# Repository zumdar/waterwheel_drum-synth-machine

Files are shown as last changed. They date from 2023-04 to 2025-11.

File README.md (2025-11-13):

# The Wacky Waterwheel Wonder Machine!

A synthesizer, drum machine, electromechanical, waterwheel powered musical intsrument!

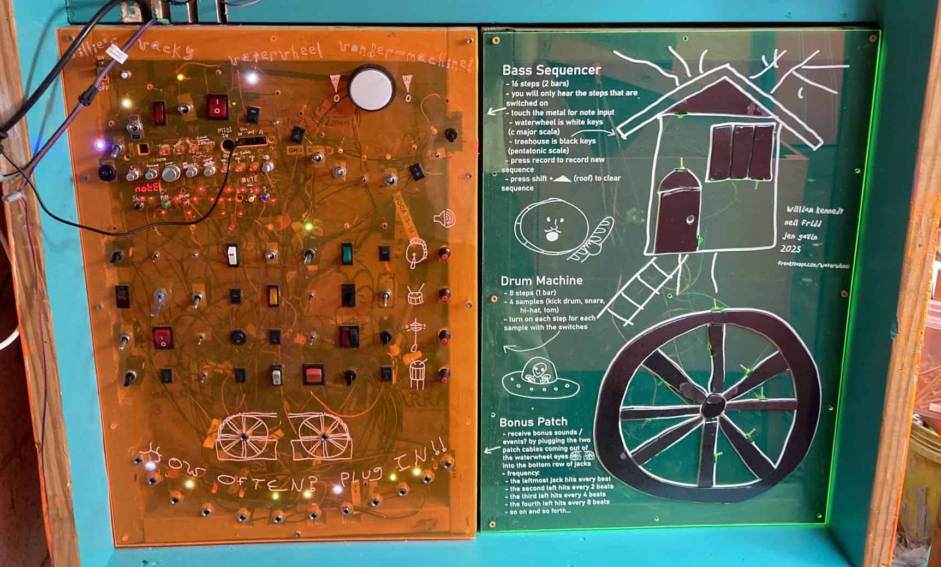
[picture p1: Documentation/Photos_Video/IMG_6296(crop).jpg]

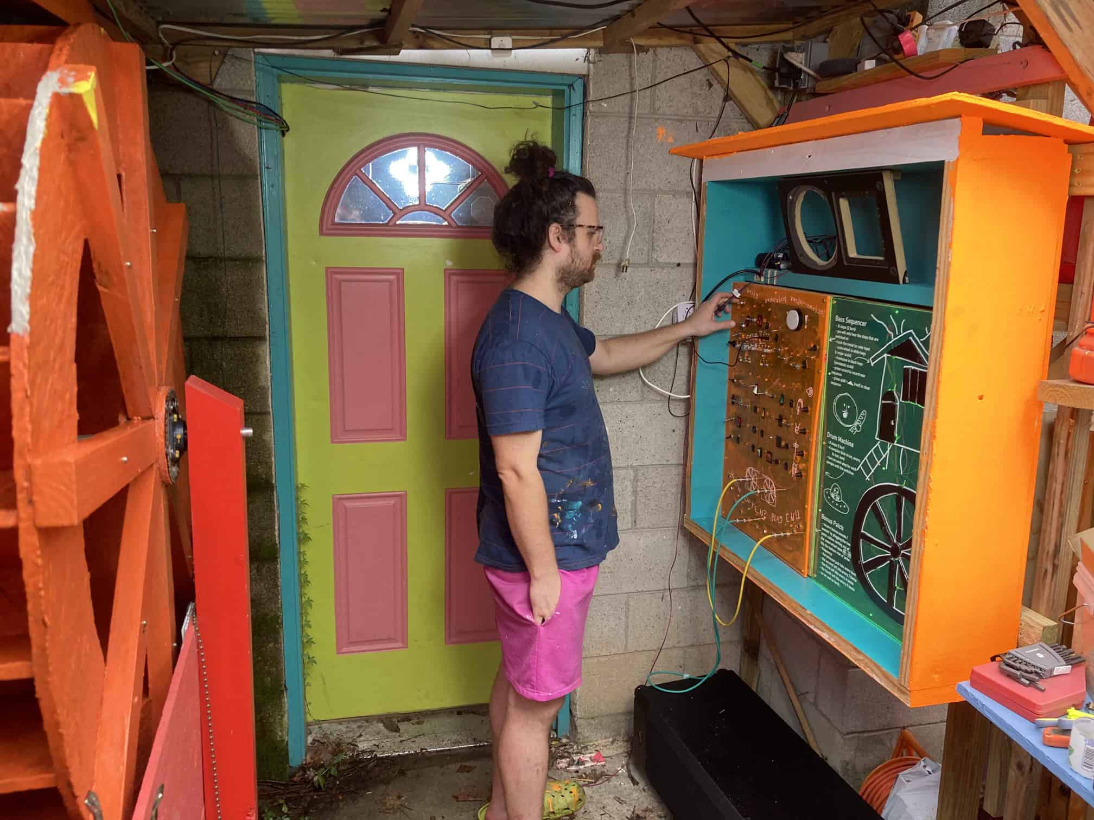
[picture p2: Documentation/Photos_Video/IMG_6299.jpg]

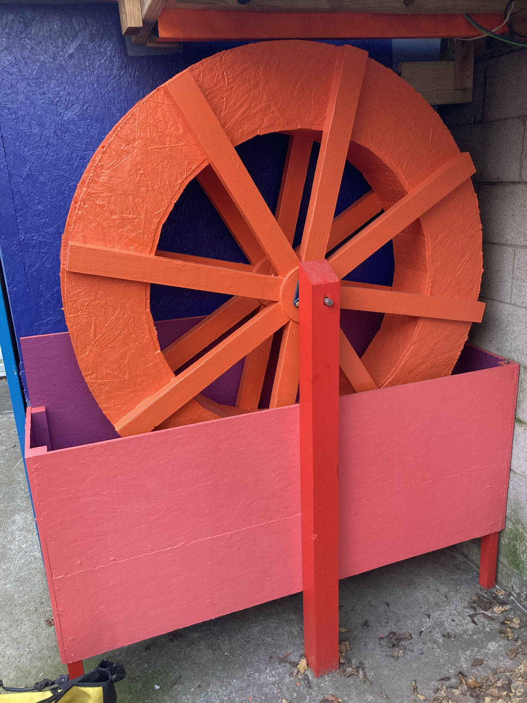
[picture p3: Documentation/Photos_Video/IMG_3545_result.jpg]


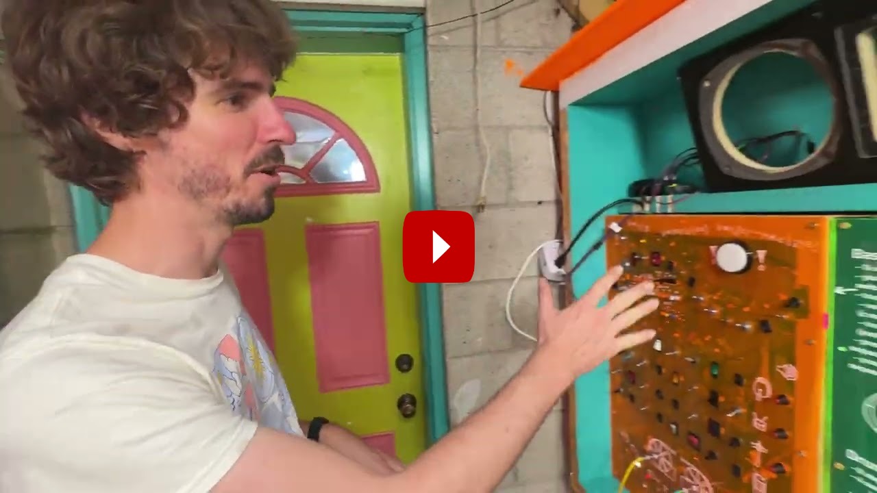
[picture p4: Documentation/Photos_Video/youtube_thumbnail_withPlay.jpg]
youtube link (https://www.youtube.com/watch?v=vC32thTY1A0)


Started in Oct. 2022 in Nashville, TN as part of The Paradise Driveway residency, full working version complete in Oct. 2025.

Project created in collaboration with

- [Neil Fridd (aka Terror Pigeon)](https://terrorpigeon.bandcamp.com/)
- [Jen Gavin (aka Paradise MIDI)](https://paradisemidi.com/)

# Overview

The Waterwheel Wondermachine is a nature powered mechanical-electronic logic idea workstation. It is a hybrid of bass synthesizer, drum machine, and kinetic motor instrument. When it rains, the waterwheel spins and every spoke of the wheel triggers the machine to advance one step of the sequence.

It has the feel of an old analog switch board or the cockpit of an airplane with 50+ toggle switches, patch cables, and LEDs scattered everywhere. Intimidating as it may look from the outside — and even more so on the inside since the front panels are translucent — the machine is simple enough where anyone can walk up and play it!

When it rains, the machine generates evolving musical sequences mixed with the percussive sounds of the external motors striking parts of the frame. When the sun returns, it transforms into a contemplative sound sculpture, droning notes played on the touch canvas panel.

You can play a melody on the waterwheel drawing, using its cleverly arranged key sequence to inspire a new variation on the original idea. All of this is contingent on the correct environmental conditions (rain), so that you have a consistent performance. The rain sounds also play a sonic role, incorporating into the spacial ambiance.

# Tech Specs

- 16 step bass synthesizer sequencer
- 8 step, 4 sample drum sequencer
- 2x motor outputs, motors mounted in the instrument area, creating sounds by clever mounting with the motors hitting parts of the frame.
- All timing and sequencing done with CD4xxx logic chips and digital circuity, a complex puzzle of logic chips, inputs and outputs and buffering.
- the note input of the synthesizer is a drawing of a waterwheel and tree house (homage to Neil s backyard). We cut these pieces out of metal and are using capacitive touch to send those notes to the synthesizer.
- 1 big sample button to trigger a sample whenever the performer wants

# PCB

## V1 - etched

- Schematic was designed in October 2022. A PCB (well 3 actually...) were designed and then etched on the driveway on copper clad FR4 board. Here is the design:
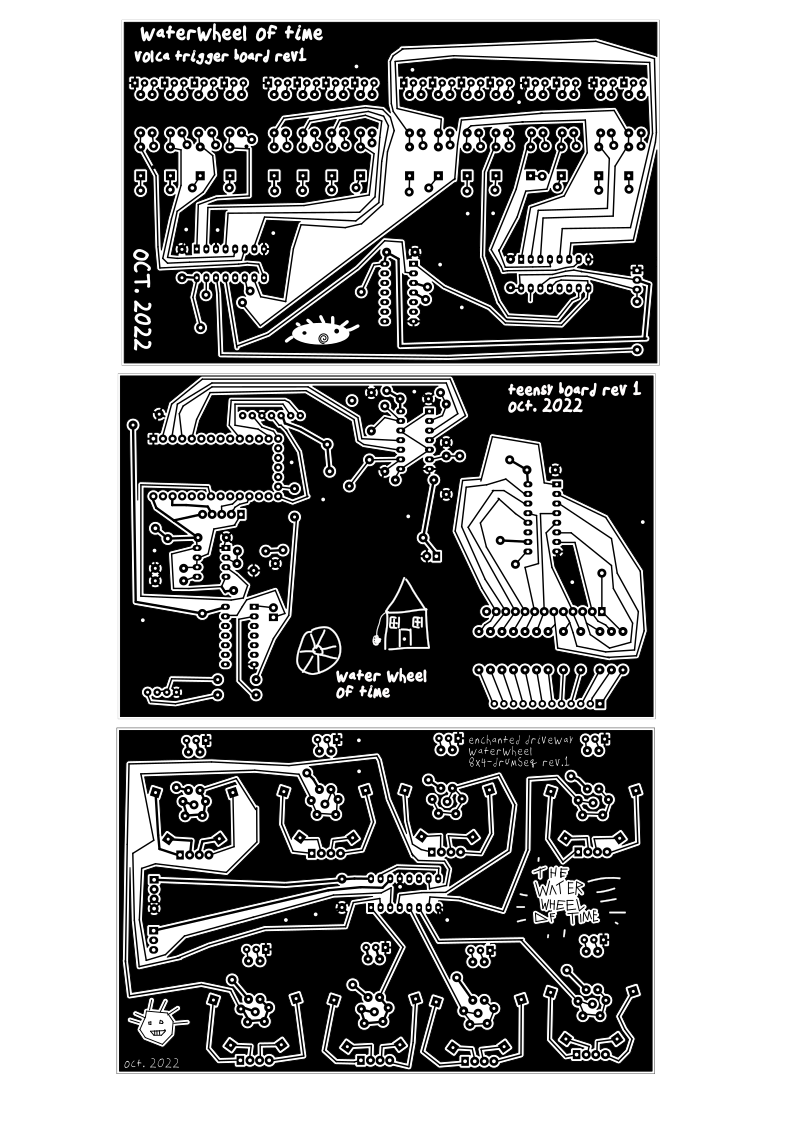
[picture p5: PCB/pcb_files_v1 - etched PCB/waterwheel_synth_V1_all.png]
  
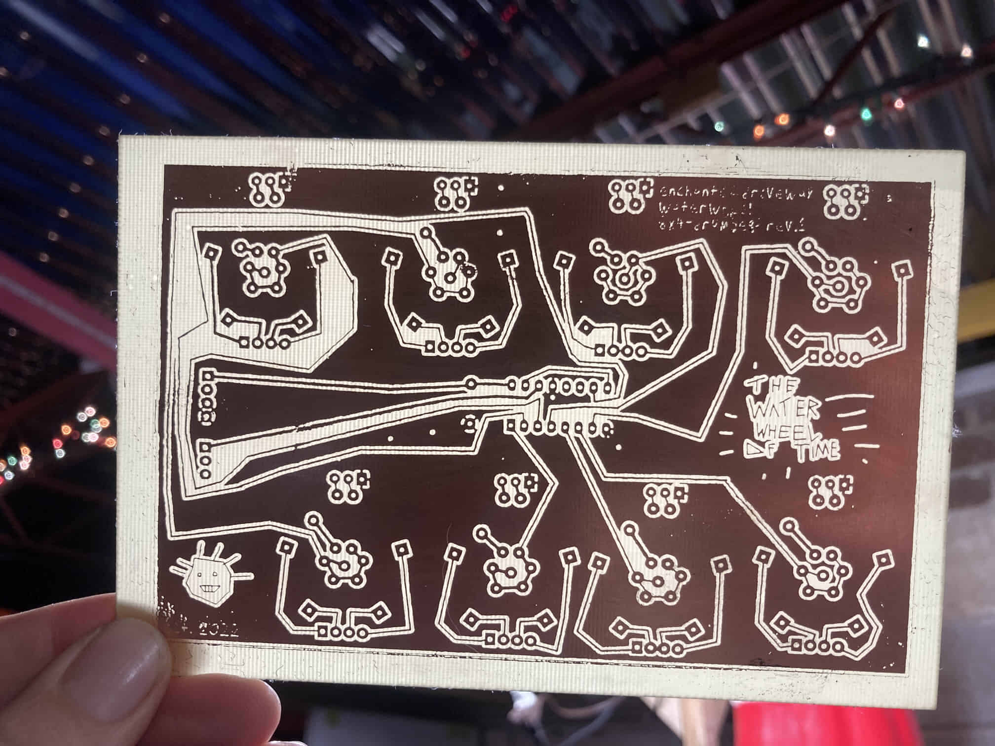
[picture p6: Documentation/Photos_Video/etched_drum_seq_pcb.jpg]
  
- The etched PCB was tested and then a full PCB was designed and fabricated by JLCPCB

## V2 - fabricated PCB

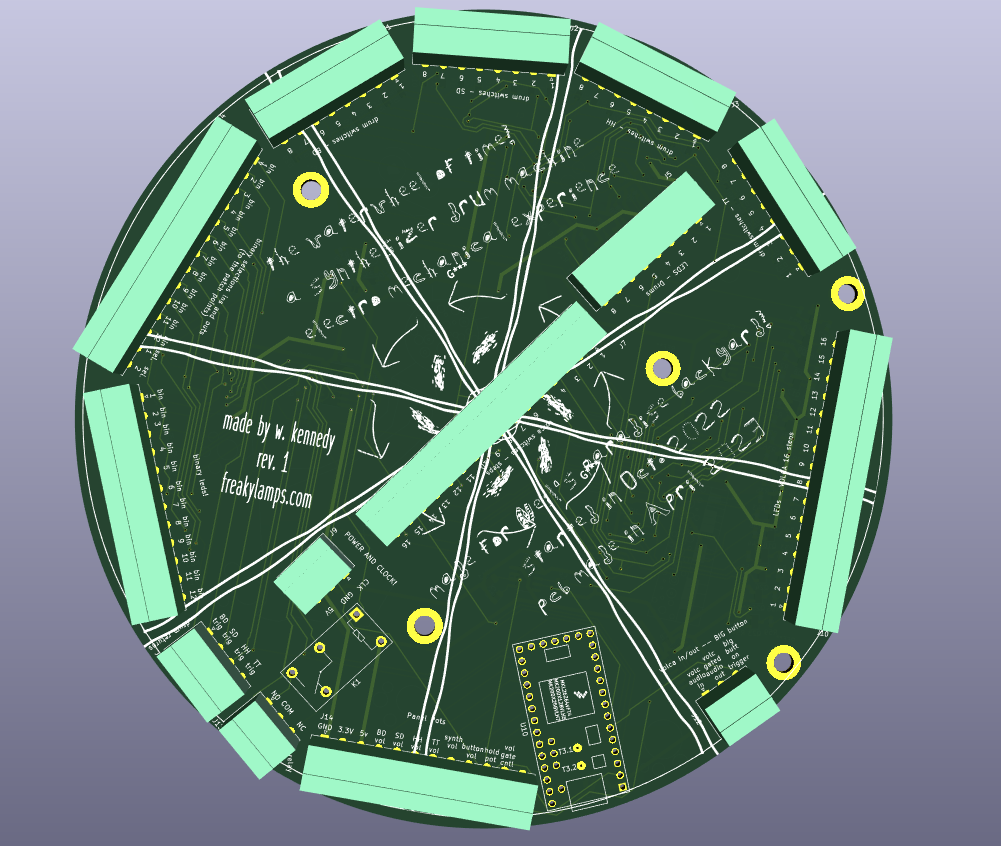
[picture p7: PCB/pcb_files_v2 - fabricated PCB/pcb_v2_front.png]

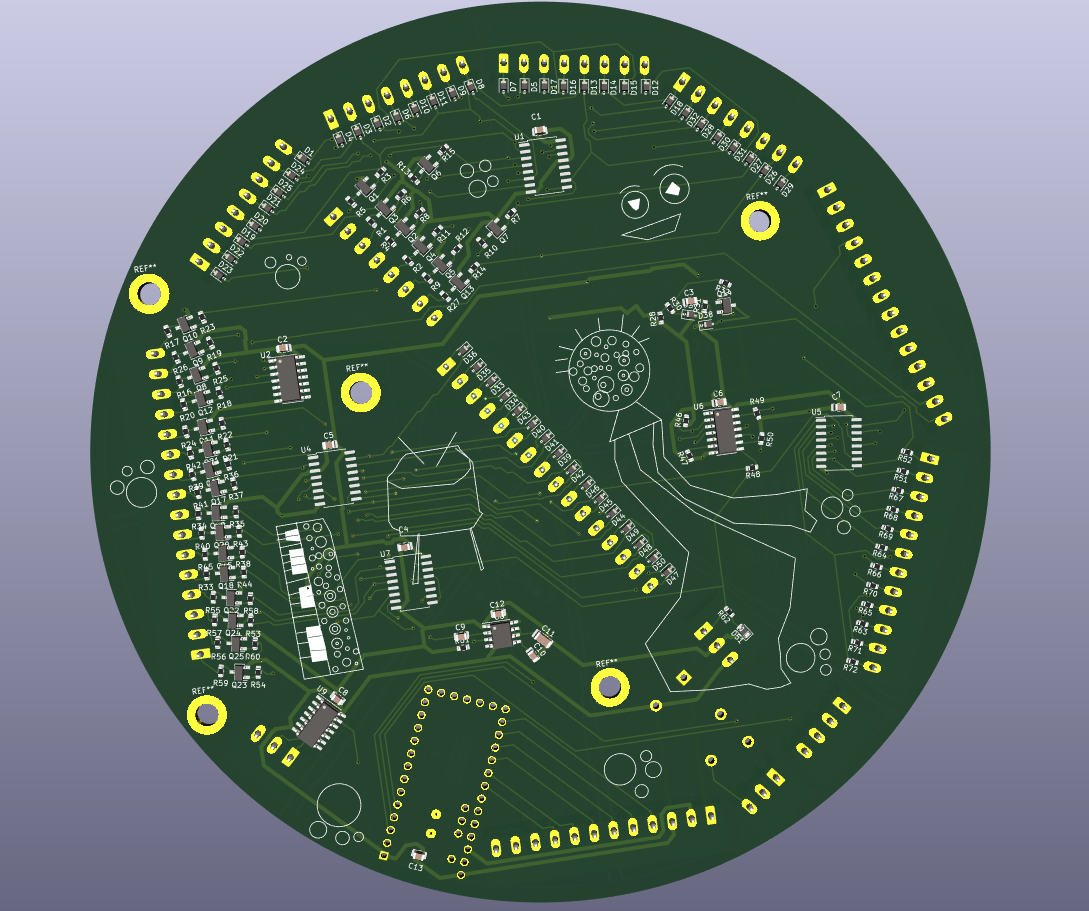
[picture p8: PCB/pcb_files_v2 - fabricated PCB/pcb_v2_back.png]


[Link to Schematic for V2](https://github.com/zumdar/waterwheel_drum-synth-machine/blob/main/PCB/pcb_files_v2%20-%20fabricated%20PCB/waterwhel_V2_SCHEMATIC.pdf)

## PCB V2 errors

- no pulldown for clock
- 555 footprint doesnt fit
- some silkscreen labels are covered up by connectors

# References

[getting trigger from sequencer - casper electronics ](https://web.archive.org/web/20130509102109/http://casperelectronics.com/2007/03/19/sequencer-update/)

[more info about multi channel 4017 sequencer/trigger - sailor mouth](https://web.archive.org/web/20160915053601/http://www.sailormouth.org/trigseq2.html)

[how to get a easy trigger with the 4017 sequecner - little gate seq - electro music forum](https://electro-music.com/forum/topic-63020.html)

[MFOS 4017 sequencer lots of good info on how it works](http://musicfromouterspace.com/analogsynth_new/TENSTEPSEQUENCER/TENSTEPSEQUENCER.php)

[classic baby 10 sequencer](https://hackaday.com/2016/01/14/oh-baby-baby10-build-a-classic-analog-music-sequencer/)

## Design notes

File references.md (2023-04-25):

# Notes about Waterwheel Synthesizer project

DAY 1
 - experiement with old Volca Keys and Bass, 
 - come up with idea for 64 switches, start working on schematic 

DAY 2 - 
- install reed switch and magnets on wheel
- tweak to get them all working
-  Prototype 4017 sequencer, 2 channel 4 steps each. 
-  need AND circuit to get triggers for each step, use 4093 NAND chip. 
- sucess with sample player with SD card! 
### research
I want sample playback for drum sounds
#### Requirements  
- needs to be quick (adafruit sound fx board takes 125ms to trigger!)
- want to change samples on the fly with sd card or IDEALLY usb stick
- No external hardware other then what i have.. no teensy audio shields
  - esp, arduino, teensy
- [teensy 4.0 sample player](https://forum.aemodular.com/thread/1214/teensy-4-sample-player) - pretty perfect except you need to do the wav to C++ conversion and upload new code for new samples....
- [teensy polyphonic samples](https://github.com/newdigate/teensy-polyphony)
- [teensy variable playback ](https://github.com/newdigate/teensy-variable-playback) - confusing library but you can play back samples.. do you need external audio shield?

## References

[getting trigger from sequencer - casper electronics ](https://web.archive.org/web/20130509102109/http://casperelectronics.com/2007/03/19/sequencer-update/)

[more info about multi channel 4017 sequencer/trigger - sailor mouth](https://web.archive.org/web/20160915053601/http://www.sailormouth.org/trigseq2.html)

[how to get a easy trigger with the 4017 sequecner - little gate seq - electro music forum](https://electro-music.com/forum/topic-63020.html)

[MFOS 4017 sequencer lots of good info on how it works](http://musicfromouterspace.com/analogsynth_new/TENSTEPSEQUENCER/TENSTEPSEQUENCER.php)

[classic baby 10 sequencer](https://hackaday.com/2016/01/14/oh-baby-baby10-build-a-classic-analog-music-sequencer/)

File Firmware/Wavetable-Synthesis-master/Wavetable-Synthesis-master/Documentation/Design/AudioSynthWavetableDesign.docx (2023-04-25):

# AudioSynthWavetable Design Specification

Project: TeensyAudio Wavetable Synthesis

Authors: Ryan Mellmer

Connor Delaplane

Aida Keifer

Nicholas Craig

Josh Bucklin

Jonathan Jensen

Xuan Tang

Date: 2016-11-28

Version: 1.0

Table of Contents

1 INTRODUCTION

1.1 Objectives

1.2 Scope

2 Functionality

2.1 Site Map

3 Architecture

3.1 Architecture Overview

3.2 Application Interfaces

4 Design

4.1 Object Diagram

5 CODE

5.1 File Names and Structure

5.2 Executable File Names and Structure

# 1 INTRODUCTION

## 1.1 Objectives

The purpose of this document is to outline the technical specifications for the Wavetable Synthesis library to be used on the Teensy 3.2 microcontroller. It is primarily meant as a guide for the developers of the library and will cover the following areas:

- Definitions of all objects within the library along with their interfaces.
- Interactions with the existing Audiostream.h library API.

## 1.2 Scope

The purpose of this project is to provide a C++ library and accompanying Python utility scripts allowing realistic instrumentation audio to be synthesized on the Teensy 3.2 Arduino Digital Analog Converter (DAC). This library will be exposed to developers, and will allow pitch shifting, looping, tremolo, and vibrato effects to be imposed on a raw byte buffer of recorded samples.

# 2 Functionality

## 2.1 Soundfont Decoding

The basic functionality of the SoundFont Decoding script is defined in the Wavetable Synthesis on Microcontroller Requirements document. A brief summary is provided here.

- User executes the script in a console
- User loads a .sf2 file into the utility by passing it’s location to the script
- If the .sf2 adheres to pre-defined limitations for what the Wavetable Library accepts, then allow the user to select which instrument to import
- Parse samples into logical units
- Output the resulting samples into a C++ struct/object within a .cpp file for use within the Wavetable Synthesis Library

## 2.2 Wavetable Synthesis Library

The basic functionality of the Wavetable Synthesis Library is defined in the Wavetable Synthesis on Microcontroller Requirements document. A brief summary is provided here.

- Load audio data from the file produced by SF2 extraction process
- Play silence in the event of read error
- Create interpolated audio data on the Teensy
- An audio sample’s sustain data can be looped
- Audio data can be modified with a tremolo effect
- Audio data can be modified with a vibrato effect

# 3 Architecture

## 3.1 Architecture Overview

SF2 file object diagram:

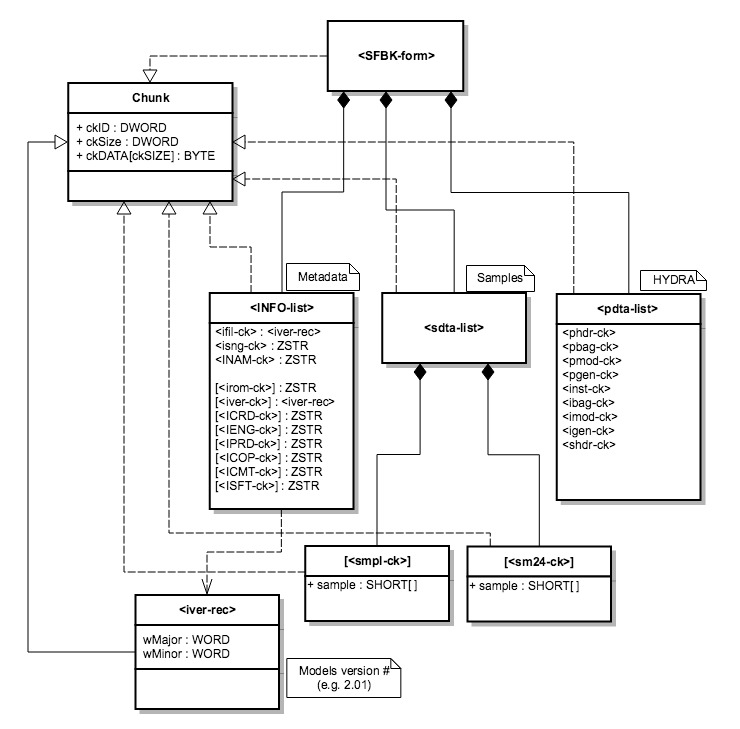
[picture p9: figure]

SoundFont Decoding:

Teensy C++ Library:

This diagram gives a general overview of how both the SF2 Decoder and the Teensy C++ Library will work together. It’s important to notice that a single Note # file generated by the SF2 Decoder will contain all three phases for a single sample (attack, sustain, release). In addition, while there is only a single arrow from the Wavetable to Teensy Sketch there could be up to 10 instances. There should be at least one Wavetable object for every note included in the Teensy Sketch file.

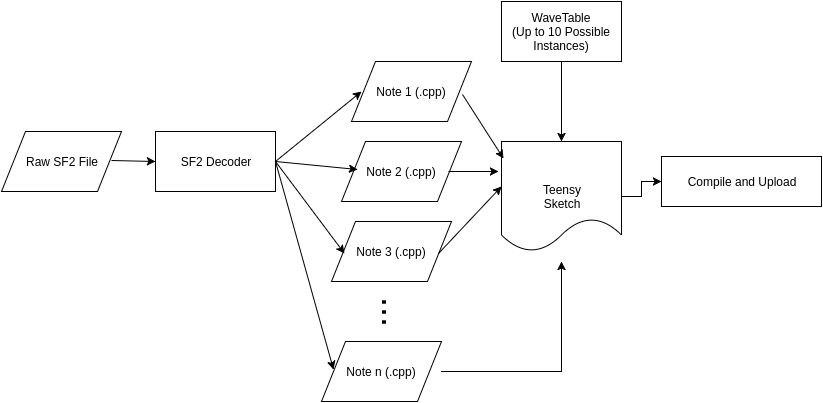
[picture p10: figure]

## 3.2 Application Interfaces

This section contains a description of all SF2 Decoding and Teensy C++ Library application interfaces.

Python SF2 Decoding:

The SoundFont decoding script will be ran only through the command-line, so the only interface to be described is the command-line. The user will need to input the location of the SoundFont file to decode, and the script will walk the user through the decoding process.

Teensy C++ Library:

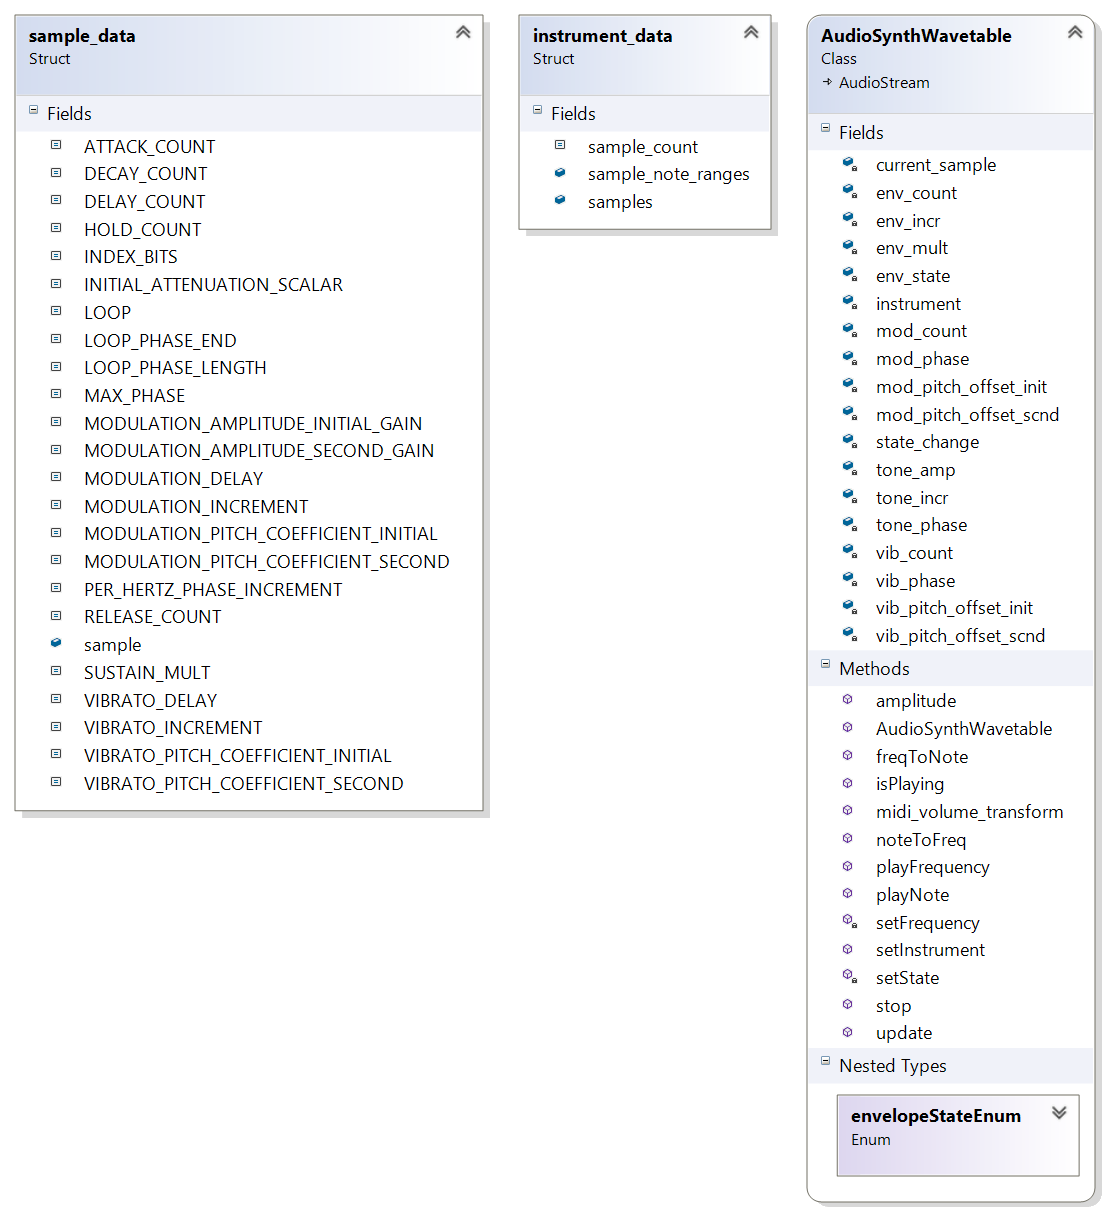
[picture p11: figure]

The AudioSynthWavetable library is made up of 3 distinct datatypes:

1. AudioSynthWavetable Class object
2. instrument_data struct
3. sample_data struct

The AudioSynthWavetable object is the main API object to interface with in order to utelize the wavetable library. This class exposes methods surrounding playing notes, changing frequency of playback, stopping notes, and setting the instrument to play. A complete description of the AudioSynthWavetable class can be found at https://teensyaudio.github.io/Wavetable-Synthesis/html/index.html

The instrument_data struct contains information which makes up a complete instrument, such as an array of samples in the form of sample_data structs, the number of samples for the instrument, and key range upper bounds for each sample within the instrument. The sample_data struct contains information surrounding a specific sample within an instrument. The sample_data information is exported and stored as algebraic expressions as to optimize and reduce the amount of processing that has to be done on the Teensy at runtime as to increase playback efficiency. A full listing of all of the fields within these structs as well as the purpose for their values can be found within the sample_data.cpp file.

# 4 Design

## 4.1 Class Diagrams

Soundfont Decoding:

The SoundFont decoding script will be contained within a single Python file. Since the script will be a purely command-line driven tool, an open source library, sf2utils, will be utilized to assist in the soundfont decoding process.

Teensy C++ Library:

The Wavetable Synthesis library consists of one primary class called AudioSynthWavetable. A class diagram that lists the fields and methods of this class is given above, and documentation for the API specifics is given at https://teensyaudio.github.io/Wavetable-Synthesis/html/index.html

This is followed by a brief description of each element within the diagram. Note: The public methods and their functionality are listed in section 3.2, Application Interfaces.

# 5 CODE

## 5.1 File Names and Structure

This section lists the name, purpose and structure of all expected files for this project.

SoundFont Decoding Utility:

File #1: decoder.py

Purpose: Main Python script file which the user will actually interact with to decode samples from a soundfont file.

Structure: This file will contain the entirety of the necessary functionality for the SF2 decoding script.

Teensy C++ Library:

File #1: AudioSynthWavetable.h

Purpose: This file contains the Wavetable class prototype and is intended to be #include(d) within any file using the Wavetable object.

Structure: This file will contain a single class prototype, Wavetable, that is derived from the AudioStream class. As such the prototype will contain the update() method along with all other fields and methods listed in the Wavetable class diagram found in section 4.1.

In addition to the class prototype the Audiostream.h library will be #include(d) so it is available for the new Wavetable class.

File #2: AudioSynthWavetable.cpp

Purpose: This file contains the implementation of all of the Wavetable class methods.

Structure: This file will #include the Wavetable.h file and will contain implementations for all public and private methods of the class.

Wavetable Synthesis Technical Specification v1.0 Page of

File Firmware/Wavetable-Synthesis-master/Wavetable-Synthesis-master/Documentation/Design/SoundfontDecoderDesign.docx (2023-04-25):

# SoundFont Decoding Functional Specification

## 1. Introduction

### 1.1. Summary

The SoundFont decoding script will be a utility included with the TeensyAudio Wavetable codebase and will allow users to pull data for various instrumentation samples from SoundFont 2 files for use by the TeensyAudio Wavetable library.

### 1.2. Requirements

See requirements documentation for detailed description of the functional requirements this document will implement.

### 1.3. Existing System

Currently this functionality isn’t available to users of the Teensy library. The script to decode SF2 files will be a brand new addition to the TeensyAudio codebase.

### 1.4. Terminology

DAC - Digital Analog Converter (the Teensy 3.2 is an example of a DAC).

SF2 - SoundFont version 2 File Format (wavetable audio data wrapped w/ synthesis methods).

Sample Array - An array or list of individual byte samples to be produced by the SoundFont decoding script for use in the TeensyAudio Wavetable library.

Attack - Portion of the decoded sample array which plays immediately upon activation (e.g. piano key depression).

Sustain - Portion of the decoded sample array which can be looped indefinitely to produce a sustaining, consistent instrument tone.

Release - Portion of the decoded sample array which plays after the sustained section of a note, and will mark the natural end of a tone.

### 1.5. References

# Wavetable Synthesis on Microcontroller Requirements.docx - Rev 115

## 2. Functional Description

Use Cases

1. Load Soundfont/SF2
  1.1. Description: User provides something for the utility to process.
  1.2. Actors: User; Soundfont;
  1.3. Entry Conditions: N/A
  1.4. Exit Conditions: Relevant contents of the Soundfont are displayed on screen in some selectable format.
  1.5. Flow:
    1.5.1. User invokes utility, specifying local file path to desired soundfont/SF2.
    1.5.2. Necessary checking for compatibility and proper file structure is done by the utility. Error and exit program if one of the following scenarios are met:
      1.5.2.1. SF2 file can’t be imported, or a file read issue occurs.
      1.5.2.2. Instrument/sample sections don’t exist within the file.
    1.5.3. Success message displayed to user if compatible.
      1.5.3.1. Failure message displayed to user if Soundfont does not meet the protocol or in the event of a File Read Error.
      1.5.3.2. Exit.
    1.5.4. Continue to Select Instrument.
2. Select Instrument
  2.1. Description: User needs to select an instrument(s) to use.
  2.2. Actors: User; Soundfont;
  2.3. Entry: Soundfont contents are displayed on screen.
  2.4. Exit: User has chosen quit, or finish.
  2.5. Flow:
    2.5.1. A prompt is displayed on screen to select an instrument, otherwise quit.
    2.5.2. User selects quit.
      2.5.2.1. Utility terminates.
    2.5.3. User inputs a selection.
      2.5.3.1. A prompt is displayed on screen to select an additional instrument, finish, or quit.
      2.5.3.2. If User selects an instrument
        2.5.3.2.1. go to 2.5.3.1
      2.5.3.3. If User selects finish
        2.5.3.3.1. Continue to Parse Samples.
      2.5.3.4. If User selects quit.
        2.5.3.4.1. Terminate utility.
3. Parse Sample(s)
  3.1. Description: User selects a sample(s) to export.
  3.2. Actors: User; Soundfont;
  3.3. Entry: Available samples are shown to the user for the selected instrument.
  3.4. Exit: User selects sample(s) to export, then the program continues to export samples.
  3.5. Flow:
    3.5.1. A prompt is displayed on screen to select an sample, otherwise quit.
    3.5.2. User selects quit.
      3.5.2.1. Utility terminates.
    3.5.3. User inputs a selection.
      3.5.3.1. Error and exit program if one of the following scenarios are met:
        3.5.3.1.1. Sample loop-end - loop-start > sample-end - sample-start (Check that the looping section is smaller than the sample itself.
        3.5.3.1.2. Sample loop-end < sample-end (Check that the sample loop end position isn’t past the end of the sample)
      3.5.3.2. If errors have occurred here, then we can potentially do some automated modification to the start and end index locations. Ask the user if they want the program to attempt to fix these issues, or quit.
      3.5.3.3. If no errors, a prompt is displayed on screen to select additional samples (if memory space on Teensy would allow so), finish, or quit.
      3.5.3.4. If User selects another sample
        3.5.3.4.1. Go to 3.5.3.1
      3.5.3.5. If User selects finish
        3.5.3.5.1. Continue to export samples.
      3.5.3.6. If User selects quit.
        3.5.3.6.1. Terminate utility.
4. Export Sample(s)
  4.1. Description: Selected samples get exported/encoded to a .cpp file with corresponding .h file, in either PCM or ulaw sound data encoding.
  4.2. Actors: User; Soundfont;
  4.3. Entry: Desired samples have been chosen for export.
  4.4. Exit: Program generates a corresponding .cpp and .h file for the selected sample contents.
  4.5. Flow:
    4.5.1. Desired sample data gets pulled from the SF2.
    4.5.2. User selects desired encoding method for sample data (options are PCM or ulaw)
    4.5.3. For each sample, write the following to a .cpp file:
      4.5.3.1. Output a struct declaration with an appropriate name for the sample.
      4.5.3.2. Within the struct, write out metadata about the sample, including sample rate, length, and frequency (if available).
      4.5.3.3. Within the struct, write out 3 separate arrays: AudioSample_Attack, AudioSample_Loop, and AudioSample_Decay. These arrays will contain sample data for all 3 different sections of the sample.
    4.5.4. Confirmation is displayed to the user with information pertaining to where the file was saved, and how many samples were exported.
    4.5.5. Program exits.

User Community
The demographic of this project is anyone wishing to extract audio data from a SoundFont 2 file. This may include musicians, programmers, audio engineers, students, and casual “tinkerers”. The primary target system for this project is the Teensy 3.2 microcontroller and its related software, particularly for the purpose of wavetable synthesis.

Error Handling

File read error: In the event that the program either cannot locate the target file, cannot properly extract audio data from the file, or finds the file to be corrupt or otherwise unusable, it will throw an exception without generating any output audio data.

Invalid instrument: If the implementation of instrument selection (described below) admits the possibility of making an invalid selection, then the input should be ignored and the user should be prompted again.

Help
Help will be accessible through the design/implementation documents and comments in code.

Interface
The user will be able to execute the script from a command line, giving an SF2 file pathname as input. Assuming the file read is successful, the user will be prompted to select from a range of instruments encoded in the file. If the selection is valid, the script will produce (along with a confirmation message) an output .cpp file with 3 unsigned int arrays containing the byte string audio data extracted from the SF2 file for the given instrument. These arrays represent the 3 sections of the SF2 audio data (attack, sustain, release).

Platforms

This software will be supported on all OSes which support SF2 and Python 2.7.

Portability
This utility should be usable by any version of Python > 2.7.

Documentation
Developer documentation to be provided to list out how to utilize this utility, as well as the different functions/options that are exposed.

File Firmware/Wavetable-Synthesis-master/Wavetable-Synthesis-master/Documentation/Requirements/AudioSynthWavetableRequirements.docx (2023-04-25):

# Software Requirements Specification

Project: TeensyAudio Wavetable Synthesis

Authors: Ryan Mellmer

Connor Delaplane

Aida Keifer

Nicholas Craig

Josh Bucklin

Jonathan Jensen

Xuan Tang

Date: 2016-11-28

Version: 1.15

Table of Contents

1.0 Introduction

1.1 Overview

1.2 Glossary

2.0 Major Components of the Solution

3.0 SoundFont Sample Extraction Script

3.1 Functional Requirements

3.2 Non-Functional Requirements

4.0 Modeling of Wavetable Synthesis Library

4.1 Functional Requirements

4.2 Non-Functional Requirements

5.0 Wavetable Synthesis Library for Teensy

5.1 Functional Requirements

5.2 Non-Functional Requirements

6.0 Minimum Viable Product

# 1.0 Introduction

### 1.1 Overview

The primary aim of this project is to produce a solution which is capable of running wavetable synthesis on both the Teensy 3.2 and Teensy 3.6 microcontroller boards. This document will define the requirements for the solution, in particular aiming for the following goals:

- Requirements should be defined so they can be easily confirmed and completed
- Individual requirements should be as independent as possible, to facilitate scheduling
- Requirements for individual parts should fit into a process of iteration

### 1.2 Glossary

Term | Definition
Wavetable Synthesis | A form of musical synthesis relying on the modification of actual instrument audio samples. This is contrasted with other forms of audio synthesis that work on fundamental waveforms.
SoundFont (SF2) | A file format capable of storing instrument samples for use in wavetable synthesis.
Teensy | USB-based microcontroller development system distributed by PJRC. (website: pjrc.com)
Delay | Portion of the decoded envelope which causes a delay before the attack section is heard.
Attack | Portion of the decoded envelope which plays immediately upon activation (e.g. piano key depression).
Hold | Portion of the decoded envelope at which the sample stays at maximum amplitude, directly following the attack.
Decay | Portion of the decoded envelope where the amplitude is decreased continually until reaching the sustain portion.
Sustain | Portion of the decoded envelope which can be looped indefinitely to produce a sustaining, consistent instrument tone at a constant amplitude.
Release | Portion of the decoded envelope which plays after the sustained section of a note, and will mark the natural end of a tone.

# 2.0 Major Components of the Solution

## Script/program to extract samples from SoundFont file

A script, written in Python with an accompanying GUI, which will take a SoundFont file and produce a C++-formatted data structure of instrument samples and sample metadata from the soundfont file for easy use in wavetable synthesis the Teensy.

## Audio library portion on the Teensy

A wavetable synthesis library written for the Teensy 3.2/Teensy 3.6 which is capable of taking the previously mentioned instrument samples and producing musical output based on interaction with its API.

# 3.0 SoundFont Sample Extraction Script

The following is a description of the behavior of a utility that will to unpack SoundFont files and generate C++ formatted data which will be used by the Teensy wavetable synthesis library.

## 3.1 Functional Requirements

### User loads valid SF2

Description: To set the stage for processing SoundFont samples, the user must provide a .sf2 for the utility.

Input: Some arbitrary .sf2 file.

Output: Confirmation to user that the input file is compatible, otherwise a notice that the file has not been accepted.

### User loads invalid SF2

Description: There are various different criteria under which an .sf2 will be rejected by the script:

- .sf2 depends on specific oscillators/effects in order to function correctly
- An individual note recording is too large to fit within the Teensy’s memory

Input: Invalid .sf2 (doesn’t conform to the above criteria)

Output: Error message explaining why the file won’t be processed.

### List contents of SF2

Description: Display to the user the contents of the loaded SoundFont in some selectable format.

Input: Verified .sf2 file.

Output: List of the instruments within the inputted SoundFont.

### User select instrument from list

Description: User selects which instrument(s) they would like to use.

Input: Some user input corresponding to the SoundFont sample they would like to use.

Output: Confirmation to user of a successful selection.

### Parse sample into a C++ formatted data structure

Description: Prepare the sample as a custom struct that is appropriate for the wavetable synthesis library, and contains all needed information/metadata that is required by the wavetable class.

Input: Successful instrument and sample selection from user.

Output: 1 .cpp file with 3 unsigned int arrays holding contents or dumping pure wav bytes to disk for the 3 logical parts of a sample (Attack, Sustain, Release).

## 3.2 Non-Functional Requirements

Size of the sample output size will be constrained such that it can be loaded onto the Teensy 3.2/Teensy 3.6. This will be an easily configurable value within the script to accommodate usage on other microcontrollers which may have more onboard memory to utilize. The user should easily be notified by the utility of how much memory the currently selected instrument samples will take up on the Teesny’s onboard memory.

# 4.0 Wavetable Synthesis Library for Teensy

This section outlines the requirements for the library features that will be created for use with Teensy & TeensyDuino. Where appropriate interface details are given.

On a high level, this library will take extracted samples encoded in a byte array as input and, through programmatic interaction with its API, produce output compatible with the Audiostream.h API of the Teensy Audio library.

## 4.1 Functional Requirements

This section describes what the new library will be able and where appropriate describes how the interface for the feature should behave by giving input/output pairs.

### Load audio data from the file produced by SF2 extraction process.

Description: In order to make audio data available for other library features (interpolation, tremolo, vibrato) the .cpp file that contains a const uint array from the SF2 extraction will be loaded and stored for repeated use by other functions within the library.

This data will be stored in a way that makes the attack, sustain and release phases of the audio sample available separately.

Input: A .cpp file that was generated by the SF2 extraction script.

Output: The three phases of the audio sample attack, sustain and release will be loaded into memory.

### Play silence in the event of read error.

Description: If the audio data can’t be loaded from a file or converted properly (interpolation, tremolo, vibrato) then the memory for the the audio samples will be filled with 0’s for silence.

Input: File with invalid data.

Output: Memory for storing attack, sustain and release is filled with 0’s.

### Create interpolated audio data on the Teensy.

Description: Given a sample of audio data, it will be converted to audio data for a different pitch using an interpolation algorithm. The exact algorithm to be used is to be determined in design/prototyping, and will largely be determined by the method which produces the highest-quality sound while still performing at a high enough rate to keep up with audio playback.

The interface to accomplish this should take in one audio sample at a time. This allows each phase of an sample to be interpolated separately.

Input: A buffer of audio data that has been loaded from memory.

Output: A buffer containing the interpolated audio data changed to a new pitch.

### An audio sample’s sustain data can be looped.

Description: When playing the attack, sustain and release phases of an audio sample the sustain phase of the sample can be looped repeatedly.

Input: Trigger the library to play a note with a duration longer than that of the raw sustain data.

Output: An unbroken output buffer filled with looping sustain data as long as the predetermined audio sustain length.

### An audio sample’s volume envelope is applied to the audio output.

Description: Using values decoded from the soundfont file, transform the output audio’s volume by applying envelope transformations at specified intervals.

Input: Interpolated audio data at a user-defined frequency.

Output: An unbroken output buffer filled with varying volume as a function of time as specified by the sample’s envelope data.

### Audio data can be modified with a tremolo effect.

Description: Given a sample of audio data it can be modified to have a tremolo effect by using a tremolo algorithm. This effect can be coupled with any other effect, including interpolation.

Input: A buffer of audio data that has been loaded from memory.

Output: A buffer of audio data that has been modified for tremolo.

### Audio data can be modified with a vibrato effect.

Description: Given a sample of audio data it can be modified to have a vibrato effect by using a vibrato algorithm. This effect can be coupled with any other effect including interpolation.

Input: A buffer of audio data that has been loaded from memory.

Output: A buffer of audio data that has been modified for vibrato.

## 4.2 Non-Functional Requirements

### Implementation in C++ as a class or set of classes

### Description: Implementation of the Wavetable Synthesis on the Teensy library will occur entirely in C++. Primarily this will facilitate interoperability with the Audiostream.h API.

### Entirety of code and sample data must fit within the Teensy’s limited on-board memory.

Description: The Teensy 3.2 DAC has 64k of on-board memory. The audio library that is produced, as well as the base instrument sample arrays must be as memory efficient as possible to conserve memory. The produced functionality should be able to run fully-functional with this amount of memory.

### Audio production must be fast, and without notable clipping.

Description: The purpose of this wavetable synthesis project is to allow users to create usable musical instruments, so the audio that is produced from the library must be free from noticeable audio clipping, and should perform in real-time as to prevent any noticeable input lag for the user. Instruments need to be responsive for their players, so this library should be held to the same standard.

### Library must be well-documented and must expose all functions necessary to utilize all features of the library.

Description: This library will mainly be used by developers who will look to use it in their own projects. To make their lives easier, the library we produce must be well documented, and has to expose all functions necessary to take full advantages of all of the libraries features.

# 5.0 Minimum Viable Product

The minimum viable product will tentatively be set as a combination of the above three components, with the following limitations:

- An attack, sustain, and release sample for a single instrument will be extracted from a SoundFont file and stored in a .cpp-based byte array
- The byte array will be loadable by both the modeling program, and the Teensy based wavetable synth library
- Both the modeling program and the library will play a single scale, using the extracted samples

This will give us a good baseline from which to add in additional functionality as per the requirements listed above in this document.

Wavetable Synthesis on a Microcontroller, PSU Computer Science Capstone, Rev. 1.15

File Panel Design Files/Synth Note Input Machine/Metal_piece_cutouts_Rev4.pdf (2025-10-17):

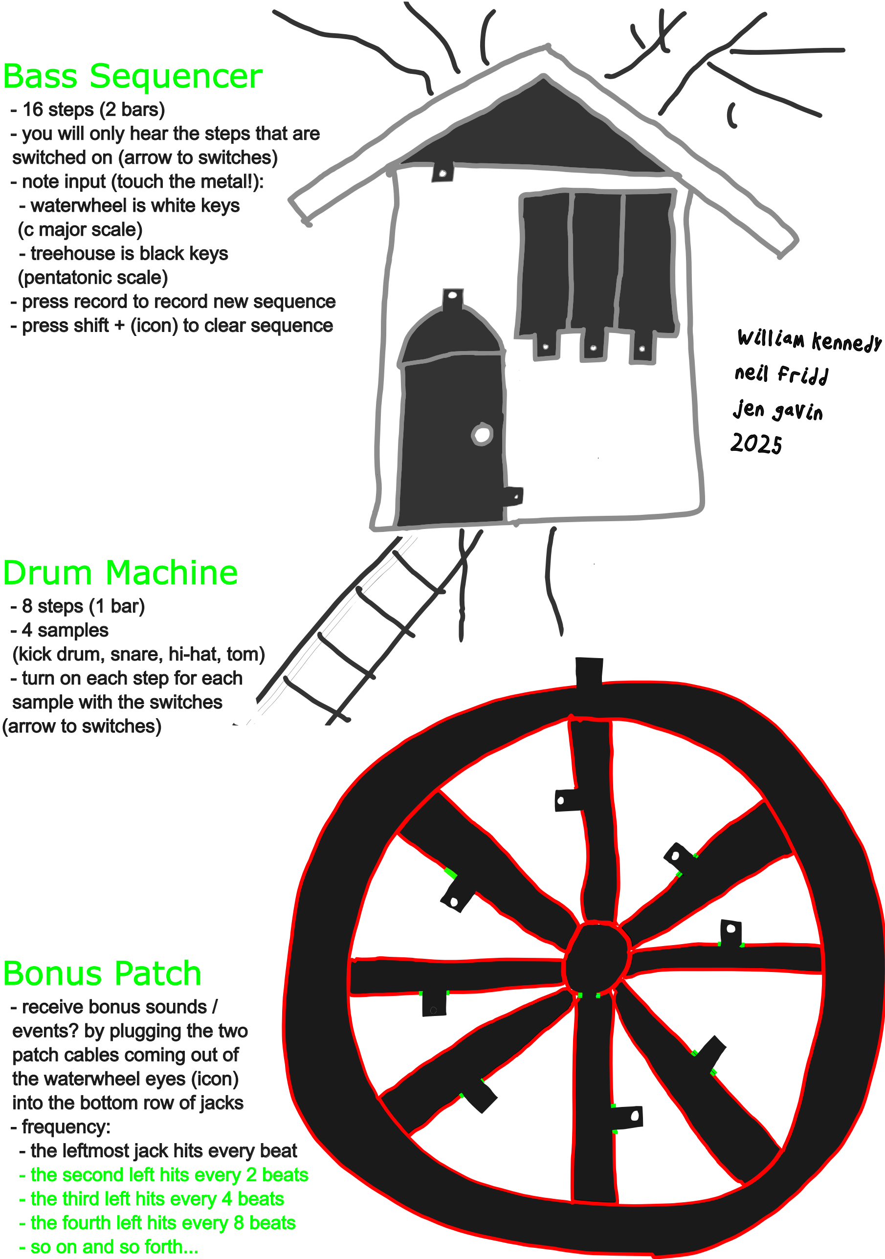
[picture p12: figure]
Bass Sequencer; - 16 steps (2 bars) - you will only hear the steps that are switched on (arrow to switches) - note input (touch the metal!): - waterwheel is white keys (c major scale) - treehouse is black keys (pentatonic scale) - press record to record new sequence; Drum Machine; - 8 steps (1 bar) - 4 samples (kick drum, snare, hi-hat, tom) - turn on each step for each sample with the switches (arrow to switches); Bonus Patch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

- press shift + (icon) to clear sequence

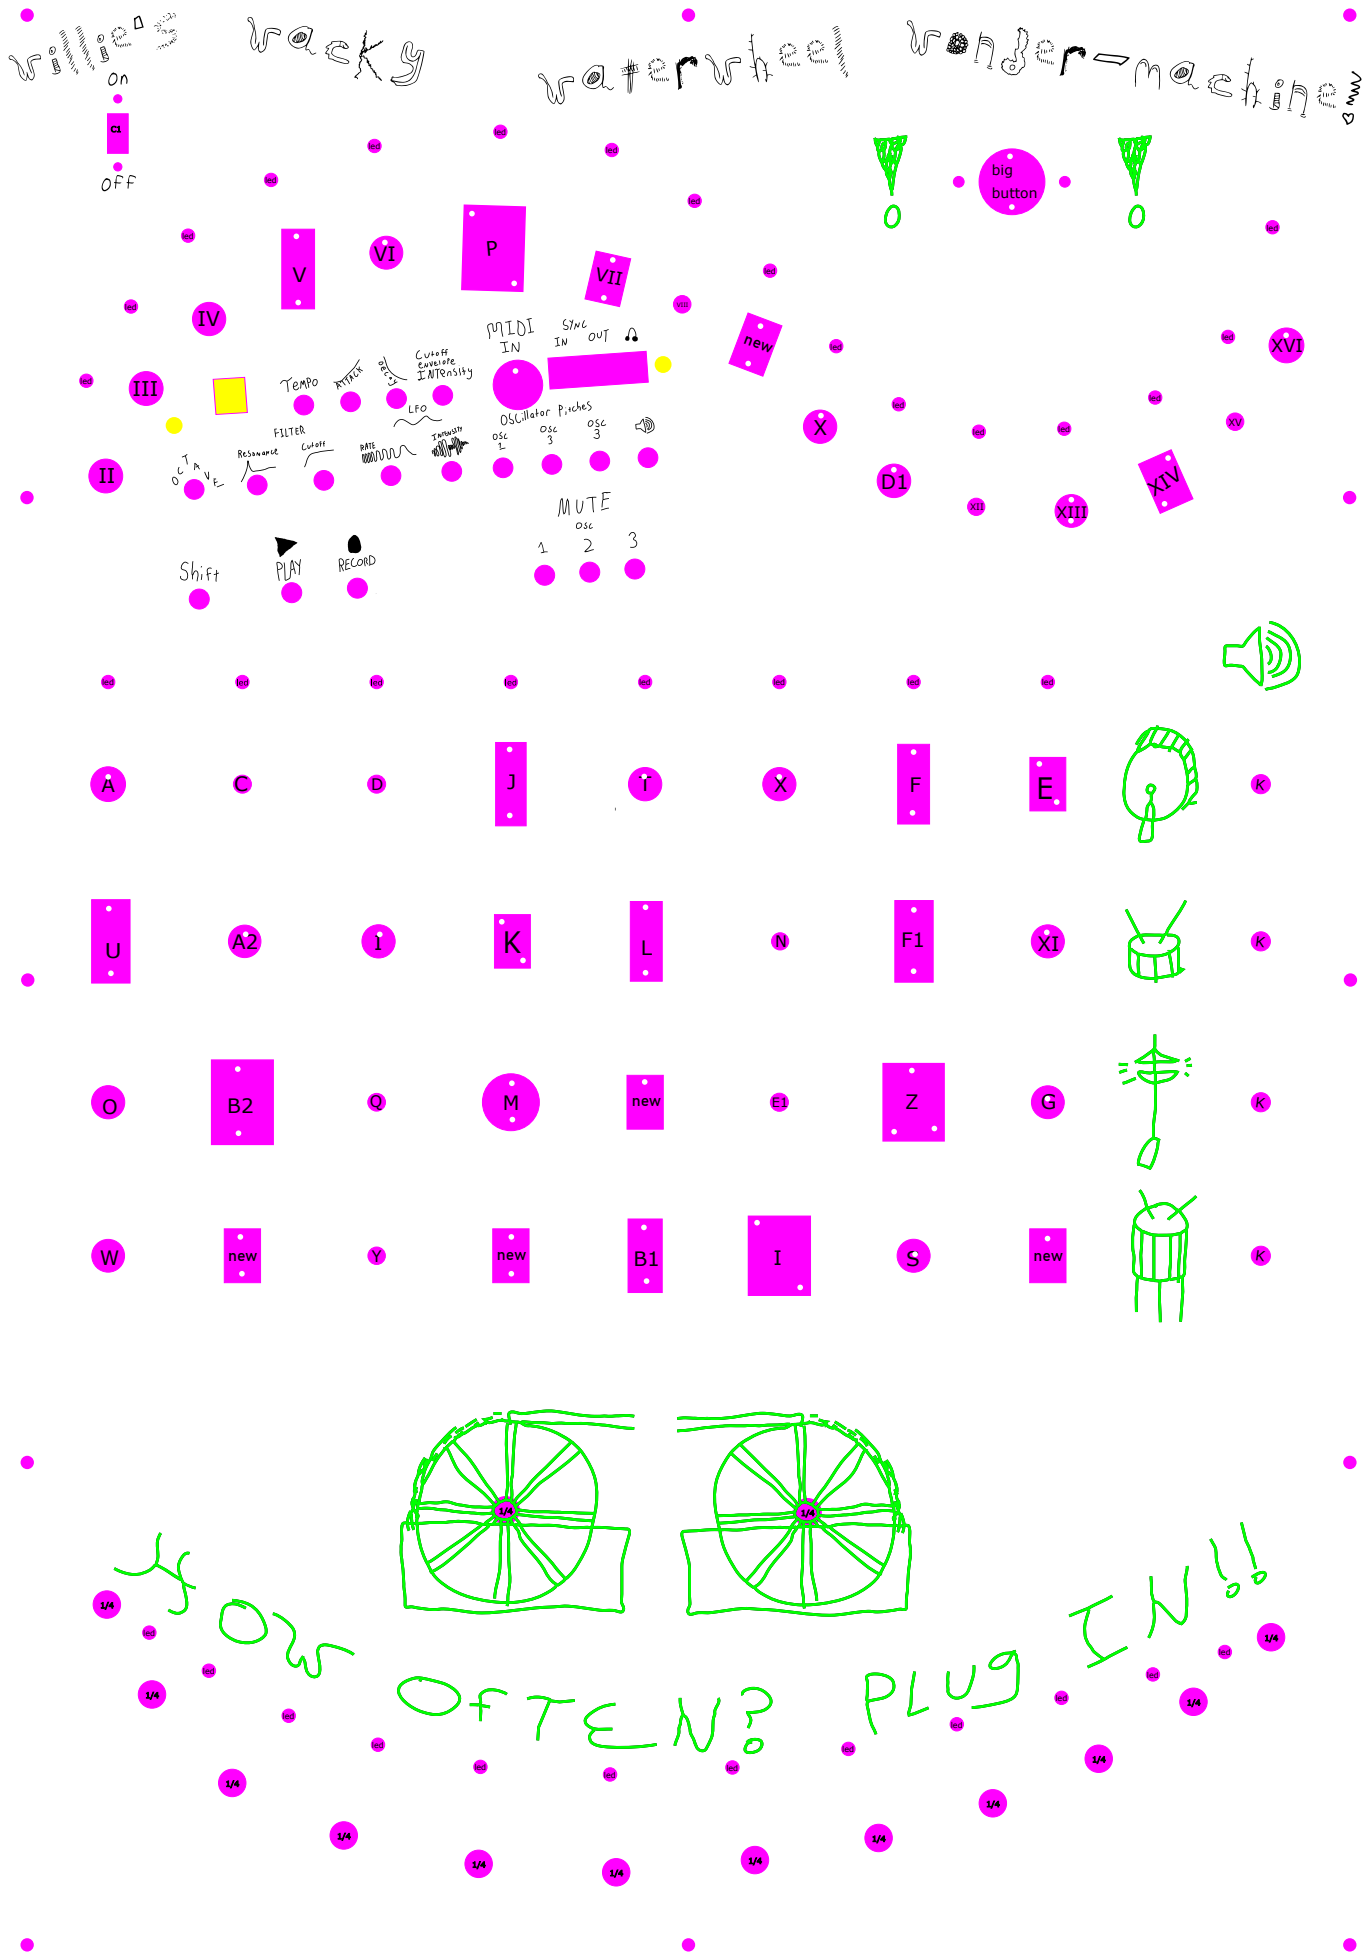
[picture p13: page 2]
led; new; big button; XII; XIII; XIV; XVI; III; VIII; VII
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

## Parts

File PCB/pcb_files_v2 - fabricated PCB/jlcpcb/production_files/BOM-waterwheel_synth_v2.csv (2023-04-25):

Comment | Designator | Footprint | LCSC
100u | C11 | C_1206_3216Metric | C15008
1k | R1,R10,R13,R16,R17,R2,R20,R24,R26,R27,R32,R33,R34,R39,R4,R40,R41,R42,R45,R5,R55,R56,R57,R59,R62,R9 | R_0603_1608Metric | C17513
4.7u | C3,C9 | C_0805_2012Metric | C1779
4069 | U2 | SO-14_3.9x8.65mm_P1.27mm | C194330
1N4148 | D1,D10,D11,D12,D13,D14,D15,D16,D17,D18,D19,D2,D20,D21,D22,D23,D24,D25,D26,D27,D28,D29,D3,D30,D31,D32,D33,D34,D35,D36,D37,D38,D39,D4,D40,D41,D42,D43,D44,D45,D46,D47,D48,D49,D5,D50,D6,D7,D8,D9 | D_SOD-323 | C2128
2N3904 | Q1,Q10,Q11,Q12,Q13,Q14,Q15,Q16,Q17,Q18,Q19,Q2,Q20,Q21,Q22,Q23,Q24,Q25,Q3,Q4,Q5,Q6,Q7,Q8,Q9 | TSOT-23 | C2146
4.7k | R48 | R_0603_1608Metric | C23162
470 | R51,R52,R63,R64,R65,R66,R67,R68,R69,R70,R71,R72 | R_0603_1608Metric | C23179
100k | R11,R12,R14,R15,R18,R19,R21,R22,R23,R25,R3,R35,R36,R37,R38,R43,R44,R53,R54,R58,R6,R60,R7,R8 | R_0603_1608Metric | C25803
10k | R46,R47,R49,R50,R61 | R_0603_1608Metric | C25804
100nf | C1,C2,C4,C5,C6,C7,C8 | C_0805_2012Metric | C28233
22k | R28,R30,R31 | R_0603_1608Metric | C31850
4040 | U5 | SO-16_5.3x10.2mm_P1.27mm | C353974
4017 | U1,U4,U7 | SO-16_5.3x10.2mm_P1.27mm | C356694
4081 | U6 | SO-14_3.9x8.65mm_P1.27mm | C40551
2.2u | C12 | C_0805_2012Metric | C49217
0.1u | C10,C13 | C_0805_2012Metric | C49678
4066 | U9 | SO-14_3.9x8.65mm_P1.27mm | C54755
555(NEW_layout) | U8 | SOIC-8_5.275x5.275mm_P1.27mm | C7593
LED | D51 | D_0805_2012Metric | C84256
RELAY out | J13 | PhoenixContact_MC_1,5_3-G-3.81_1x03_P3.81mm_Horizontal
volc audio in/out. button trig | J12 | PhoenixContact_MC_1,5_3-G-3.81_1x03_P3.81mm_Horizontal
Drum_Returns | J11 | PhoenixContact_MC_1,5_4-G-3.81_1x04_P3.81mm_Horizontal
LEDS_volca | J10 | PhoenixContact_MC_1,5_16-G-3.81_1x16_P3.81mm_Horizontal
power and clock | J9 | PhoenixContact_MC_1,5_3-G-3.81_1x03_P3.81mm_Horizontal
LED_binary | J8 | PhoenixContact_MC_1,5_12-G-3.81_1x12_P3.81mm_Horizontal
Volca_steps | J7 | PhoenixContact_MC_1,5_16-G-3.81_1x16_P3.81mm_Horizontal
Drum_sw_TT | J6 | PhoenixContact_MC_1,5_8-G-3.81_1x08_P3.81mm_Horizontal
LED_drums | J5 | PhoenixContact_MC_1,5_8-G-3.81_1x08_P3.81mm_Horizontal
12x binary outs, 2x ins | J4 | PhoenixContact_MC_1,5_14-G-3.81_1x14_P3.81mm_Horizontal
Drum_sw_HH | J3 | PhoenixContact_MC_1,5_8-G-3.81_1x08_P3.81mm_Horizontal
Drum_SW_SD | J2 | PhoenixContact_MC_1,5_8-G-3.81_1x08_P3.81mm_Horizontal
Drum_SW_BD | J1 | PhoenixContact_MC_1,5_8-G-3.81_1x08_P3.81mm_Horizontal
Teensy3.2 | U10 | Teensy30_31_32_LC
G5Q-1 | K1 | Relay_SPDT_Omron-G5Q-1
panel pots | J14 | PhoenixContact_MC_1,5_12-G-3.81_1x12_P3.81mm_Horizontal

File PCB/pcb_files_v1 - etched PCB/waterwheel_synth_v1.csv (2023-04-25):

Source: | C:\Users\moogtron 4k\Desktop\projects\waterwheel synthesizer\waterwheel_synth\waterwheel_synth_v1.sch
Date: | Thu 10/20/2022 3:26:07 AM
Tool: | Eeschema (5.1.4)-1
Generator: | C:\Program Files\KiCad\bin\scripting\plugins/bom_csv_grouped_by_value.py
Component Count: | 185
Individual Components:
Item | Qty | Reference(s) | Value | LibPart | Footprint | Datasheet
 |  | C1 | 100nf | Device:C_Small |  | ~
 |  | C2 | 100nf | Device:C_Small |  | ~
 |  | C3 | 100nf | Device:C_Small |  | ~
 |  | D1 | LED | Device:LED |  | ~
 |  | D2 | LED | Device:LED |  | ~
 |  | D3 | LED | Device:LED |  | ~
 |  | D4 | LED | Device:LED |  | ~
 |  | D5 | LED | Device:LED |  | ~
 |  | D6 | LED | Device:LED |  | ~
 |  | D7 | LED | Device:LED |  | ~
 |  | D8 | LED | Device:LED |  | ~
 |  | D9 | LED | Device:LED |  | ~
 |  | D10 | LED | Device:LED |  | ~
 |  | D11 | LED | Device:LED |  | ~
 |  | D12 | LED | Device:LED |  | ~
 |  | D13 | LED | Device:LED |  | ~
 |  | D14 | LED | Device:LED |  | ~
 |  | D15 | LED | Device:LED |  | ~
 |  | D16 | LED | Device:LED |  | ~
 |  | D17 | 1N4148 | Diode:1N4148 | Diode_THT:D_DO-35_SOD27_P7.62mm_Horizontal | https://assets.nexperia.com/documents/data-sheet/1N4148_1N4448.pdf
 |  | D18 | 1N4148 | Diode:1N4148 | Diode_THT:D_DO-35_SOD27_P7.62mm_Horizontal | https://assets.nexperia.com/documents/data-sheet/1N4148_1N4448.pdf
 |  | D19 | 1N4148 | Diode:1N4148 | Diode_THT:D_DO-35_SOD27_P7.62mm_Horizontal | https://assets.nexperia.com/documents/data-sheet/1N4148_1N4448.pdf
 |  | D20 | 1N4148 | Diode:1N4148 | Diode_THT:D_DO-35_SOD27_P7.62mm_Horizontal | https://assets.nexperia.com/documents/data-sheet/1N4148_1N4448.pdf
 |  | D21 | 1N4148 | Diode:1N4148 | Diode_THT:D_DO-35_SOD27_P7.62mm_Horizontal | https://assets.nexperia.com/documents/data-sheet/1N4148_1N4448.pdf
 |  | D22 | 1N4148 | Diode:1N4148 | Diode_THT:D_DO-35_SOD27_P7.62mm_Horizontal | https://assets.nexperia.com/documents/data-sheet/1N4148_1N4448.pdf
 |  | D23 | 1N4148 | Diode:1N4148 | Diode_THT:D_DO-35_SOD27_P7.62mm_Horizontal | https://assets.nexperia.com/documents/data-sheet/1N4148_1N4448.pdf
 |  | D24 | 1N4148 | Diode:1N4148 | Diode_THT:D_DO-35_SOD27_P7.62mm_Horizontal | https://assets.nexperia.com/documents/data-sheet/1N4148_1N4448.pdf
 |  | D25 | 1N4148 | Diode:1N4148 | Diode_THT:D_DO-35_SOD27_P7.62mm_Horizontal | https://assets.nexperia.com/documents/data-sheet/1N4148_1N4448.pdf
 |  | D26 | 1N4148 | Diode:1N4148 | Diode_THT:D_DO-35_SOD27_P7.62mm_Horizontal | https://assets.nexperia.com/documents/data-sheet/1N4148_1N4448.pdf
 |  | D27 | 1N4148 | Diode:1N4148 | Diode_THT:D_DO-35_SOD27_P7.62mm_Horizontal | https://assets.nexperia.com/documents/data-sheet/1N4148_1N4448.pdf
 |  | D28 | 1N4148 | Diode:1N4148 | Diode_THT:D_DO-35_SOD27_P7.62mm_Horizontal | https://assets.nexperia.com/documents/data-sheet/1N4148_1N4448.pdf
 |  | D29 | 1N4148 | Diode:1N4148 | Diode_THT:D_DO-35_SOD27_P7.62mm_Horizontal | https://assets.nexperia.com/documents/data-sheet/1N4148_1N4448.pdf
 |  | D30 | 1N4148 | Diode:1N4148 | Diode_THT:D_DO-35_SOD27_P7.62mm_Horizontal | https://assets.nexperia.com/documents/data-sheet/1N4148_1N4448.pdf
 |  | D31 | 1N4148 | Diode:1N4148 | Diode_THT:D_DO-35_SOD27_P7.62mm_Horizontal | https://assets.nexperia.com/documents/data-sheet/1N4148_1N4448.pdf
 |  | D32 | 1N4148 | Diode:1N4148 | Diode_THT:D_DO-35_SOD27_P7.62mm_Horizontal | https://assets.nexperia.com/documents/data-sheet/1N4148_1N4448.pdf
 |  | D33 | 1N4148 | Diode:1N4148 | Diode_THT:D_DO-35_SOD27_P7.62mm_Horizontal | https://assets.nexperia.com/documents/data-sheet/1N4148_1N4448.pdf
 |  | D34 | 1N4148 | Diode:1N4148 | Diode_THT:D_DO-35_SOD27_P7.62mm_Horizontal | https://assets.nexperia.com/documents/data-sheet/1N4148_1N4448.pdf
 |  | D35 | 1N4148 | Diode:1N4148 | Diode_THT:D_DO-35_SOD27_P7.62mm_Horizontal | https://assets.nexperia.com/documents/data-sheet/1N4148_1N4448.pdf
 |  | D36 | 1N4148 | Diode:1N4148 | Diode_THT:D_DO-35_SOD27_P7.62mm_Horizontal | https://assets.nexperia.com/documents/data-sheet/1N4148_1N4448.pdf
 |  | D37 | 1N4148 | Diode:1N4148 | Diode_THT:D_DO-35_SOD27_P7.62mm_Horizontal | https://assets.nexperia.com/documents/data-sheet/1N4148_1N4448.pdf
 |  | D38 | 1N4148 | Diode:1N4148 | Diode_THT:D_DO-35_SOD27_P7.62mm_Horizontal | https://assets.nexperia.com/documents/data-sheet/1N4148_1N4448.pdf
 |  | D39 | 1N4148 | Diode:1N4148 | Diode_THT:D_DO-35_SOD27_P7.62mm_Horizontal | https://assets.nexperia.com/documents/data-sheet/1N4148_1N4448.pdf
 |  | D40 | 1N4148 | Diode:1N4148 | Diode_THT:D_DO-35_SOD27_P7.62mm_Horizontal | https://assets.nexperia.com/documents/data-sheet/1N4148_1N4448.pdf
 |  | D41 | 1N4148 | Diode:1N4148 | Diode_THT:D_DO-35_SOD27_P7.62mm_Horizontal | https://assets.nexperia.com/documents/data-sheet/1N4148_1N4448.pdf
 |  | D42 | 1N4148 | Diode:1N4148 | Diode_THT:D_DO-35_SOD27_P7.62mm_Horizontal | https://assets.nexperia.com/documents/data-sheet/1N4148_1N4448.pdf
 |  | D43 | 1N4148 | Diode:1N4148 | Diode_THT:D_DO-35_SOD27_P7.62mm_Horizontal | https://assets.nexperia.com/documents/data-sheet/1N4148_1N4448.pdf
 |  | D44 | 1N4148 | Diode:1N4148 | Diode_THT:D_DO-35_SOD27_P7.62mm_Horizontal | https://assets.nexperia.com/documents/data-sheet/1N4148_1N4448.pdf
 |  | D45 | 1N4148 | Diode:1N4148 | Diode_THT:D_DO-35_SOD27_P7.62mm_Horizontal | https://assets.nexperia.com/documents/data-sheet/1N4148_1N4448.pdf
 |  | D46 | 1N4148 | Diode:1N4148 | Diode_THT:D_DO-35_SOD27_P7.62mm_Horizontal | https://assets.nexperia.com/documents/data-sheet/1N4148_1N4448.pdf
 |  | D47 | 1N4148 | Diode:1N4148 | Diode_THT:D_DO-35_SOD27_P7.62mm_Horizontal | https://assets.nexperia.com/documents/data-sheet/1N4148_1N4448.pdf
 |  | D48 | 1N4148 | Diode:1N4148 | Diode_THT:D_DO-35_SOD27_P7.62mm_Horizontal | https://assets.nexperia.com/documents/data-sheet/1N4148_1N4448.pdf
 |  | D49 | 1N4148 | Diode:1N4148 | Diode_THT:D_DO-35_SOD27_P7.62mm_Horizontal | https://assets.nexperia.com/documents/data-sheet/1N4148_1N4448.pdf
 |  | D50 | 1N4148 | Diode:1N4148 | Diode_THT:D_DO-35_SOD27_P7.62mm_Horizontal | https://assets.nexperia.com/documents/data-sheet/1N4148_1N4448.pdf
 |  | D51 | 1N4148 | Diode:1N4148 | Diode_THT:D_DO-35_SOD27_P7.62mm_Horizontal | https://assets.nexperia.com/documents/data-sheet/1N4148_1N4448.pdf
 |  | D52 | 1N4148 | Diode:1N4148 | Diode_THT:D_DO-35_SOD27_P7.62mm_Horizontal | https://assets.nexperia.com/documents/data-sheet/1N4148_1N4448.pdf
 |  | D53 | 1N4148 | Diode:1N4148 | Diode_THT:D_DO-35_SOD27_P7.62mm_Horizontal | https://assets.nexperia.com/documents/data-sheet/1N4148_1N4448.pdf
 |  | D54 | 1N4148 | Diode:1N4148 | Diode_THT:D_DO-35_SOD27_P7.62mm_Horizontal | https://assets.nexperia.com/documents/data-sheet/1N4148_1N4448.pdf
 |  | D55 | 1N4148 | Diode:1N4148 | Diode_THT:D_DO-35_SOD27_P7.62mm_Horizontal | https://assets.nexperia.com/documents/data-sheet/1N4148_1N4448.pdf
 |  | D56 | 1N4148 | Diode:1N4148 | Diode_THT:D_DO-35_SOD27_P7.62mm_Horizontal | https://assets.nexperia.com/documents/data-sheet/1N4148_1N4448.pdf
 |  | D57 | LED | Device:LED |  | ~
 |  | D58 | LED | Device:LED |  | ~
 |  | D59 | LED | Device:LED |  | ~
 |  | D60 | LED | Device:LED |  | ~
 |  | D61 | LED | Device:LED |  | ~
 |  | D62 | LED | Device:LED |  | ~
 |  | D63 | LED | Device:LED |  | ~
 |  | D64 | LED | Device:LED |  | ~
 |  | D65 | 1N4148 | Diode:1N4148 | Diode_THT:D_DO-35_SOD27_P7.62mm_Horizontal | https://assets.nexperia.com/documents/data-sheet/1N4148_1N4448.pdf
 |  | D66 | 1N4148 | Diode:1N4148 | Diode_THT:D_DO-35_SOD27_P7.62mm_Horizontal | https://assets.nexperia.com/documents/data-sheet/1N4148_1N4448.pdf
 |  | D67 | 1N4148 | Diode:1N4148 | Diode_THT:D_DO-35_SOD27_P7.62mm_Horizontal | https://assets.nexperia.com/documents/data-sheet/1N4148_1N4448.pdf
 |  | D68 | 1N4148 | Diode:1N4148 | Diode_THT:D_DO-35_SOD27_P7.62mm_Horizontal | https://assets.nexperia.com/documents/data-sheet/1N4148_1N4448.pdf
 |  | D69 | 1N4148 | Diode:1N4148 | Diode_THT:D_DO-35_SOD27_P7.62mm_Horizontal | https://assets.nexperia.com/documents/data-sheet/1N4148_1N4448.pdf
 |  | D70 | 1N4148 | Diode:1N4148 | Diode_THT:D_DO-35_SOD27_P7.62mm_Horizontal | https://assets.nexperia.com/documents/data-sheet/1N4148_1N4448.pdf
 |  | D71 | 1N4148 | Diode:1N4148 | Diode_THT:D_DO-35_SOD27_P7.62mm_Horizontal | https://assets.nexperia.com/documents/data-sheet/1N4148_1N4448.pdf
 |  | D72 | 1N4148 | Diode:1N4148 | Diode_THT:D_DO-35_SOD27_P7.62mm_Horizontal | https://assets.nexperia.com/documents/data-sheet/1N4148_1N4448.pdf
 |  | D73 | 1N4148 | Diode:1N4148 | Diode_THT:D_DO-35_SOD27_P7.62mm_Horizontal | https://assets.nexperia.com/documents/data-sheet/1N4148_1N4448.pdf
 |  | D74 | 1N4148 | Diode:1N4148 | Diode_THT:D_DO-35_SOD27_P7.62mm_Horizontal | https://assets.nexperia.com/documents/data-sheet/1N4148_1N4448.pdf
 |  | D75 | 1N4148 | Diode:1N4148 | Diode_THT:D_DO-35_SOD27_P7.62mm_Horizontal | https://assets.nexperia.com/documents/data-sheet/1N4148_1N4448.pdf
 |  | D76 | 1N4148 | Diode:1N4148 | Diode_THT:D_DO-35_SOD27_P7.62mm_Horizontal | https://assets.nexperia.com/documents/data-sheet/1N4148_1N4448.pdf
 |  | D77 | 1N4148 | Diode:1N4148 | Diode_THT:D_DO-35_SOD27_P7.62mm_Horizontal | https://assets.nexperia.com/documents/data-sheet/1N4148_1N4448.pdf
 |  | D78 | 1N4148 | Diode:1N4148 | Diode_THT:D_DO-35_SOD27_P7.62mm_Horizontal | https://assets.nexperia.com/documents/data-sheet/1N4148_1N4448.pdf
 |  | D79 | 1N4148 | Diode:1N4148 | Diode_THT:D_DO-35_SOD27_P7.62mm_Horizontal | https://assets.nexperia.com/documents/data-sheet/1N4148_1N4448.pdf
 |  | D80 | 1N4148 | Diode:1N4148 | Diode_THT:D_DO-35_SOD27_P7.62mm_Horizontal | https://assets.nexperia.com/documents/data-sheet/1N4148_1N4448.pdf
 |  | D81 | 1N4148 | Diode:1N4148 | Diode_THT:D_DO-35_SOD27_P7.62mm_Horizontal | https://assets.nexperia.com/documents/data-sheet/1N4148_1N4448.pdf
 |  | D82 | 1N4148 | Diode:1N4148 | Diode_THT:D_DO-35_SOD27_P7.62mm_Horizontal | https://assets.nexperia.com/documents/data-sheet/1N4148_1N4448.pdf
 |  | D83 | 1N4148 | Diode:1N4148 | Diode_THT:D_DO-35_SOD27_P7.62mm_Horizontal | https://assets.nexperia.com/documents/data-sheet/1N4148_1N4448.pdf
 |  | D84 | 1N4148 | Diode:1N4148 | Diode_THT:D_DO-35_SOD27_P7.62mm_Horizontal | https://assets.nexperia.com/documents/data-sheet/1N4148_1N4448.pdf
 |  | D85 | 1N4148 | Diode:1N4148 | Diode_THT:D_DO-35_SOD27_P7.62mm_Horizontal | https://assets.nexperia.com/documents/data-sheet/1N4148_1N4448.pdf
 |  | D86 | 1N4148 | Diode:1N4148 | Diode_THT:D_DO-35_SOD27_P7.62mm_Horizontal | https://assets.nexperia.com/documents/data-sheet/1N4148_1N4448.pdf
 |  | D87 | 1N4148 | Diode:1N4148 | Diode_THT:D_DO-35_SOD27_P7.62mm_Horizontal | https://assets.nexperia.com/documents/data-sheet/1N4148_1N4448.pdf
 |  | D88 | 1N4148 | Diode:1N4148 | Diode_THT:D_DO-35_SOD27_P7.62mm_Horizontal | https://assets.nexperia.com/documents/data-sheet/1N4148_1N4448.pdf
 |  | J1 | Screw_Terminal_01x02 | Connector:Screw_Terminal_01x02 |  | ~
 |  | J2 | Screw_Terminal_01x02 | Connector:Screw_Terminal_01x02 |  | ~
 |  | R1 | 1k | Device:R_Small_US |  | ~
 |  | R2 | 1k | Device:R_Small_US |  | ~
 |  | R3 | 1k | Device:R_Small_US |  | ~
 |  | R4 | 1k | Device:R_Small_US |  | ~
 |  | R5 | 1k | Device:R_Small_US |  | ~
 |  | R6 | 1k | Device:R_Small_US |  | ~
 |  | R7 | 1k | Device:R_Small_US |  | ~
 |  | R8 | 1k | Device:R_Small_US |  | ~
 |  | R9 | 1k | Device:R_Small_US |  | ~
 |  | R10 | 1k | Device:R_Small_US |  | ~
 |  | R11 | 1k | Device:R_Small_US |  | ~
 |  | R12 | 1k | Device:R_Small_US |  | ~
 |  | R13 | 1k | Device:R_Small_US |  | ~
 |  | R14 | 1k | Device:R_Small_US |  | ~
 |  | R15 | 1k | Device:R_Small_US |  | ~
 |  | R16 | 1k | Device:R_Small_US |  | ~
 |  | R17 | 1k | Device:R_Small_US |  | ~
 |  | R18 | 1k | Device:R_Small_US |  | ~
 |  | R19 | 1k | Device:R_Small_US |  | ~
 |  | R20 | 1k | Device:R_Small_US |  | ~
 |  | R21 | 1k | Device:R_Small_US |  | ~
 |  | R22 | 1k | Device:R_Small_US |  | ~
 |  | R23 | 1k | Device:R_Small_US |  | ~
 |  | R24 | 1k | Device:R_Small_US |  | ~
 |  | SW1 | SW_SPST | Switch:SW_SPST |  | ~
 |  | SW2 | SW_SPST | Switch:SW_SPST |  | ~
 |  | SW3 | SW_SPST | Switch:SW_SPST |  | ~
 |  | SW4 | SW_SPST | Switch:SW_SPST |  | ~
 |  | SW5 | SW_SPST | Switch:SW_SPST |  | ~
 |  | SW6 | SW_SPST | Switch:SW_SPST |  | ~
 |  | SW7 | SW_SPST | Switch:SW_SPST |  | ~
 |  | SW8 | SW_SPST | Switch:SW_SPST |  | ~
 |  | SW9 | SW_SPST | Switch:SW_SPST |  | ~
 |  | SW10 | SW_SPST | Switch:SW_SPST |  | ~
 |  | SW11 | SW_SPST | Switch:SW_SPST |  | ~
 |  | SW12 | SW_SPST | Switch:SW_SPST |  | ~
 |  | SW13 | SW_SPST | Switch:SW_SPST |  | ~
 |  | SW14 | SW_SPST | Switch:SW_SPST |  | ~
 |  | SW15 | SW_SPST | Switch:SW_SPST |  | ~
 |  | SW16 | SW_SPST | Switch:SW_SPST |  | ~
 |  | SW17 | SW_SPST | Switch:SW_SPST |  | ~
 |  | SW18 | SW_SPST | Switch:SW_SPST |  | ~
 |  | SW19 | SW_SPST | Switch:SW_SPST |  | ~
 |  | SW20 | SW_SPST | Switch:SW_SPST |  | ~
 |  | SW21 | SW_SPST | Switch:SW_SPST |  | ~
 |  | SW22 | SW_SPST | Switch:SW_SPST |  | ~
 |  | SW23 | SW_SPST | Switch:SW_SPST |  | ~
 |  | SW24 | SW_SPST | Switch:SW_SPST |  | ~
 |  | SW25 | SW_SPST | Switch:SW_SPST |  | ~
 |  | SW26 | SW_SPST | Switch:SW_SPST |  | ~
 |  | SW27 | SW_SPST | Switch:SW_SPST |  | ~
 |  | SW28 | SW_SPST | Switch:SW_SPST |  | ~
 |  | SW29 | SW_SPST | Switch:SW_SPST |  | ~
 |  | SW30 | SW_SPST | Switch:SW_SPST |  | ~
 |  | SW31 | SW_SPST | Switch:SW_SPST |  | ~
 |  | SW32 | SW_SPST | Switch:SW_SPST |  | ~
 |  | SW33 | SW_SPST | Switch:SW_SPST |  | ~
 |  | SW34 | SW_SPST | Switch:SW_SPST |  | ~
 |  | SW35 | SW_SPST | Switch:SW_SPST |  | ~
 |  | SW36 | SW_SPST | Switch:SW_SPST |  | ~
 |  | SW37 | SW_SPST | Switch:SW_SPST |  | ~
 |  | SW38 | SW_SPST | Switch:SW_SPST |  | ~
 |  | SW39 | SW_SPST | Switch:SW_SPST |  | ~
 |  | SW40 | SW_SPST | Switch:SW_SPST |  | ~
 |  | SW41 | SW_SPST | Switch:SW_SPST |  | ~
 |  | SW42 | SW_SPST | Switch:SW_SPST |  | ~
 |  | SW43 | SW_SPST | Switch:SW_SPST |  | ~
 |  | SW44 | SW_SPST | Switch:SW_SPST |  | ~
 |  | SW45 | SW_SPST | Switch:SW_SPST |  | ~
 |  | SW46 | SW_SPST | Switch:SW_SPST |  | ~
 |  | SW47 | SW_SPST | Switch:SW_SPST |  | ~
 |  | SW48 | SW_SPST | Switch:SW_SPST |  | ~
 |  | SW49 | SW_SPST | Switch:SW_SPST |  | ~
 |  | SW50 | SW_SPST | Switch:SW_SPST |  | ~
 |  | SW51 | SW_SPST | Switch:SW_SPST |  | ~
 |  | SW52 | SW_SPST | Switch:SW_SPST |  | ~
 |  | SW53 | SW_SPST | Switch:SW_SPST |  | ~
 |  | SW54 | SW_SPST | Switch:SW_SPST |  | ~
 |  | SW55 | SW_SPST | Switch:SW_SPST |  | ~
 |  | SW56 | SW_SPST | Switch:SW_SPST |  | ~
 |  | SW57 | SW_SPST | Switch:SW_SPST |  | ~
 |  | SW58 | SW_SPST | Switch:SW_SPST |  | ~
 |  | SW59 | SW_SPST | Switch:SW_SPST |  | ~
 |  | SW60 | SW_SPST | Switch:SW_SPST |  | ~
 |  | SW61 | SW_SPST | Switch:SW_SPST |  | ~
 |  | SW62 | SW_SPST | Switch:SW_SPST |  | ~
 |  | SW63 | SW_SPST | Switch:SW_SPST |  | ~
 |  | SW64 | SW_SPST | Switch:SW_SPST |  | ~
 |  | U1 | 4069 | 4xxx:4069 |  | http://www.intersil.com/content/dam/Intersil/documents/cd40/cd4069ubms.pdf
 |  | U2 | 4017 | 4xxx:4017 |  | http://www.intersil.com/content/dam/Intersil/documents/cd40/cd4017bms-22bms.pdf
 |  | U3 | 4017 | 4xxx:4017 |  | http://www.intersil.com/content/dam/Intersil/documents/cd40/cd4017bms-22bms.pdf
 |  | U4 | 4017 | 4xxx:4017 |  | http://www.intersil.com/content/dam/Intersil/documents/cd40/cd4017bms-22bms.pdf
Collated Components:
Item | Qty | Reference(s) | Value | LibPart | Footprint | Datasheet
1 | 3 | C1, C2, C3 | 100nf | Device:C_Small |  | ~
2 | 24 | D1, D2, D3, D4, D5, D6, D7, D8, D9, D10, D11, D12, D13, D14, D15, D16, D57, D58, D59, D60, D61, D62, D63, D64 | LED | Device:LED |  | ~
3 | 64 | D17, D18, D19, D20, D21, D22, D23, D24, D25, D26, D27, D28, D29, D30, D31, D32, D33, D34, D35, D36, D37, D38, D39, D40, D41, D42, D43, D44, D45, D46, D47, D48, D49, D50, D51, D52, D53, D54, D55, D56, D65, D66, D67, D68, D69, D70, D71, D72, D73, D74, D75, D76, D77, D78, D79, D80, D81, D82, D83, D84, D85, D86, D87, D88 | 1N4148 | Diode:1N4148 | Diode_THT:D_DO-35_SOD27_P7.62mm_Horizontal | https://assets.nexperia.com/documents/data-sheet/1N4148_1N4448.pdf
4 | 2 | J1, J2 | Screw_Terminal_01x02 | Connector:Screw_Terminal_01x02 |  | ~
5 | 24 | R1, R2, R3, R4, R5, R6, R7, R8, R9, R10, R11, R12, R13, R14, R15, R16, R17, R18, R19, R20, R21, R22, R23, R24 | 1k | Device:R_Small_US |  | ~
6 | 64 | SW1, SW2, SW3, SW4, SW5, SW6, SW7, SW8, SW9, SW10, SW11, SW12, SW13, SW14, SW15, SW16, SW17, SW18, SW19, SW20, SW21, SW22, SW23, SW24, SW25, SW26, SW27, SW28, SW29, SW30, SW31, SW32, SW33, SW34, SW35, SW36, SW37, SW38, SW39, SW40, SW41, SW42, SW43, SW44, SW45, SW46, SW47, SW48, SW49, SW50, SW51, SW52, SW53, SW54, SW55, SW56, SW57, SW58, SW59, SW60, SW61, SW62, SW63, SW64 | SW_SPST | Switch:SW_SPST |  | ~
7 | 1 | U1 | 4069 | 4xxx:4069 |  | http://www.intersil.com/content/dam/Intersil/documents/cd40/cd4069ubms.pdf
8 | 3 | U2, U3, U4 | 4017 | 4xxx:4017 |  | http://www.intersil.com/content/dam/Intersil/documents/cd40/cd4017bms-22bms.pdf

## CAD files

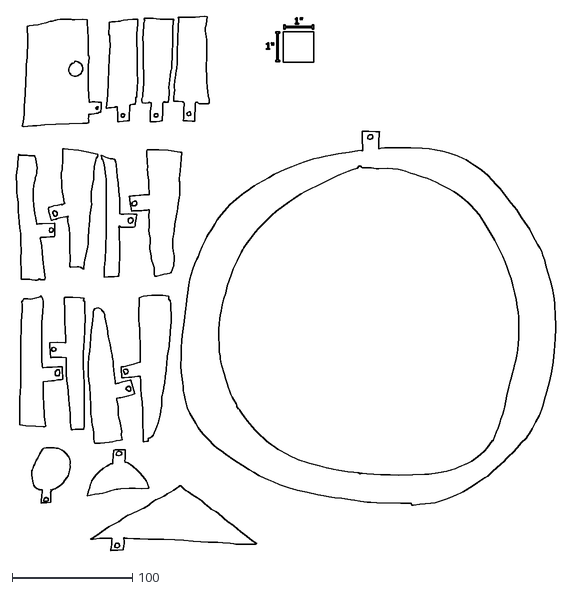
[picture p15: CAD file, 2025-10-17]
Panel Design Files/Synth Note Input Machine/Metal_piece_cutouts.dxf
447.7 x 443.4

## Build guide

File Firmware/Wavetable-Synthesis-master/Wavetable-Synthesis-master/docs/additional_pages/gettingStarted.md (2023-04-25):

# Getting started

This is a short guide on how to get started using the Audio Synth Wavetable library. 

# What is the Audio Synth Wavetable library? {#WhatIs}

The Audio Synth Wavetable is a C++ library uses sound data from a decoded SoundFont file and creates sound using wavetable synthesis. This library is for [Teensy 3.2/3.6](https://www.pjrc.com/teensy/).

# How do I use the Audio Synth Wavetable library? {#howtoUse}

To use the Audio Synth Wavetable library you must include the header file in your Arduino sketch (a `.ino` file): 

~~~~~~~~~~~~~~~{.c}
#include <AudioSynthWavetable.h>
~~~~~~~~~~~~~~~

The `AudioSynthWavetable.h` and `AudioSynthWavetable.cpp` files need to be in your Arduino library folder.

# Decoding Soundfont Files {#decoder}

See [SoundFont Decoder User-Guide](https://teensyaudio.github.io/Wavetable-Synthesis/html/md_additional_pages_soundfont_decoder.html) for
information on how to decode a .sf2 file to a usable format for the `AudioSynthWavetable` class.

# Including a Soundfont File in an Arduino Sketch {#including}

When creating a sketch that uses the `AudioSynthWavetable` class, the output files from the soundfont decoder
(in the form of .cpp and .h files) need to be placed in the same directory as the Arduino sketch. Once 
these files are in the same directory, within the Arduino sketch code, `#include "<instrument-name>_samples.h"`
must be added to the top of the sketch in order to use it with the wavetable class.

# Locating the instrument_data Within the Decoded Files {#locating}

An instance of the `AudioSynthWavetable` object requires a complete `instrument_data` object to be passed to the
wavetable object. The instrument_data object can be found in the `<instrument-name>_samples.h` file that was included from 
the output files from the SoundfontDecoder (see [`Including a Soundfont File in an Arduino Sketch`](#including) above).

# Setting up an AudioSynthWavetable Object {#settingObject}

## Audio Connections {#AudioConnectios}

Before using an AudioSynthWavetable Object to synthesize music, it will be necessary to set up some audio connection
objects. See the Teensy Audio Library documentation at https://www.pjrc.com/teensy/td_libs_Audio.html for information
on using AudioConnection objects to connect the AudioSynthWavetable object to mixers and audio output drivers for
your specific Teensy board.

## Setting an Object's Instrument {#settingInst}

To set an object's instrument, be sure that the .h and .cpp files from the SoundfontDecoder have been included in 
your Arduino sketch, and locate the name of the instrument_data object in the `<instrument-name>_samples.h` file. For
example it will look something like this for an instrument named "BasicFlute1":

~~~~~~~~~~~~~~~{.c}
const instrument_data BasicFlute1 = {2, BasicFlute1_ranges, BasicFlute1_samples };
~~~~~~~~~~~~~~~

In this example, assume that `%AudioSynthWavetable wavetable;` is already placed in the variable declaration section of the Arduino
sketch, and assume the instrument_data object that gets passed to the AudioSynthWavetable object is named `BasicFlute1`.
To set the instrument of a particular wavetable object, perform the following:

~~~~~~~~~~~~~~~{.c}
wavetable.setInstrument(BasicFlute1);
~~~~~~~~~~~~~~~

Now, the wavetable's instrument has been set, and the object can now be used to synthesize instrument sounds.

# A very simple first program {#firstProg}

This program is meant to be played using the Teensy development board that has a button on pin 1, and analog knobs on A2 and A3.

Frequency and amplitude are modified using the knobs, and the flute is triggered to play/stop via the button on pin #1.

~~~~~~~~~~~~~~~{.c}
#include <Bounce.h>
#include <Audio.h>
#include <Wire.h>
#include <SPI.h>
#include <SD.h>
#include <SerialFlash.h>

#include <AudioSynthWavetable.h>
#include "BasicFlute1_samples.h"

AudioSynthWavetable wavetable;
AudioOutputI2S i2s1;
AudioMixer4 mixer;
AudioConnection patchCord1(wavetable, 0, mixer, 0);
AudioConnection          patchCord2(mixer, 0, i2s1, 0);
AudioConnection          patchCord3(mixer, 0, i2s1, 1);
AudioControlSGTL5000 sgtl5000_1;

// Bounce objects to read pushbuttons 
Bounce button0 = Bounce(0, 15);
Bounce button1 = Bounce(1, 15);  // 15 ms debounce time
Bounce button2 = Bounce(2, 15);

void setup() { 
  Serial.begin(115200);
  pinMode(0, INPUT_PULLUP);
  pinMode(1, INPUT_PULLUP);
  pinMode(2, INPUT_PULLUP);
  AudioMemory(20);
  sgtl5000_1.enable();
  sgtl5000_1.volume(0.8);
  mixer.gain(0, 0.7);
  
  wavetable.setInstrument(BasicFlute1);
  wavetable.amplitude(1);
}

bool playing = false;

void loop() {
  // Update all the button objects
  button0.update();
  button1.update();
  button2.update();
  //Read knob values
  int knob1 = analogRead(A3);
  int knob2 = analogRead(A2);
  //Get frequency and gain from knobs
  float freq = (float)knob1/5.0;
  float gain = (float)knob2/1023.0;
  //Set a low-limit to the gain
  if (gain < .05) gain = .05;

  if (button1.fallingEdge()) {
    if (playing) {
      playing = false;
      wavetable.stop();
    }
    else {
      playing = true;
      wavetable.playFrequency(freq);
      wavetable.amplitude(gain);
    }    
  }
  wavetable.amplitude(gain);
  wavetable.setFrequency(freq);
}
~~~~~~~~~~~~~~~

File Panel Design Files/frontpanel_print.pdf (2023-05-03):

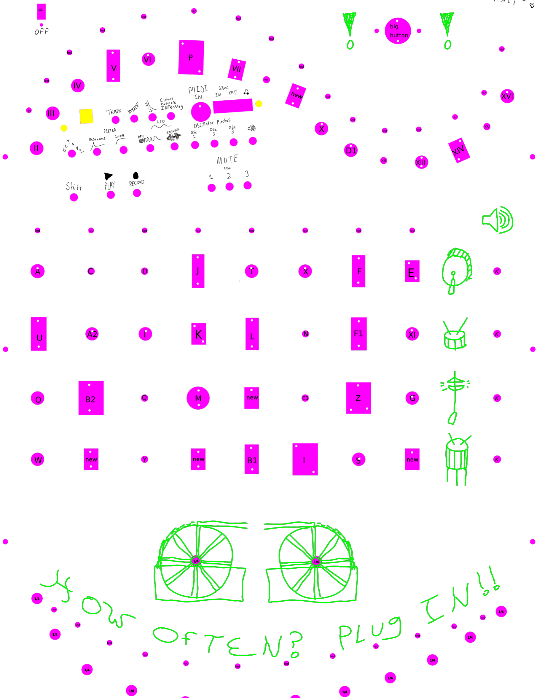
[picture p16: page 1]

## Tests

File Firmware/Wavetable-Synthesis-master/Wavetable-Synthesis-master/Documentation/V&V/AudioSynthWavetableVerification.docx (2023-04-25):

# TeensyAudio Wavetable Synthesis

# Software Verification and Validation Plan

Authors: Ryan Mellmer, Connor Delaplane | Date: 2/9/2017

# 1 Introduction

## 1.1 Purpose

The purpose of this document is to outline how the TeensyAudio Wavetable class and accompanying SoundFont decoder utility will be verified as “correct” and fulfilling the software’s functional and technical needs.

# 2 Testing Approach

The AudioSynthWavetable C++ library will be validated using two “Test Sketches”, containing code to thoroughly test the following functionality on the Teensy for correctness in pitch-interpolation and enveloping as well as benchmarking tests for performance. These sketches will be uploaded to the Teensy, and test results will be printed to the Arduino Serial Monitor.

The first sketch is called Unit_Interp and is responsible for testing correctness of the interpolation algorithm. The second, Unit_Main, performs all other tests. These tests can easily be performed selectively by simply commenting out #define [test] statements corresponding to tests that a user does not wish to perform. The interpolation test is kept in a separate sketch because it is memory- and processor-intensive.

## 2.1 Component Testing

    2.1.1 Interpolation

In order to test our interpolation functionality, we will develop a test sketch called Unit_Interp which will instantiate an instance of the AudioSynthWavetable class, and iteratively play a range of different notes using a simple sine wave as the input to the wavetable object, and then check that the output frequency is the expected frequency for whatever note we triggered, within some allowed margin of error. Using the YIN fundamental frequency estimator algorithm as implemented by Colin Duffy within the AudioAnalyzeNoteFrequency class, we are able to analyze the raw audio output frequency with high accuracy, provided the input waveform is simple. Therefore, we will be using a simple sine wave as the input “instrument” sample to the AudioSynthWavetable object because this is the simplest waveform to approximate output frequency for, and will produce the most accurate result. Results of each note test will be printed to the serial monitor. Final test results will be displayed after running all individual note tests.

The frequency analyzer object only works reliably (given an appropriately simple input waveform) for frequencies between about 0.029 and 4.0 kHz, corresponding to MIDI notes 22 and 107, respectively. As such, we will only test notes in this range. Furthermore, for ease of automated testing, the algorithm only tests notes in the western scale (12-note octaves). This corresponds exactly to the standard MIDI range, so this suffices for our purposes.

Test Pseudocode

The following is high-level pseudocode for the basic operation of Unit_Interp.

for (each note in [22 - 107]) {

input_frequency := frequencyOf(note)

playNote(note)

while (note has been playing for less than 500 milliseconds)

output_frequency := getOutputFreq()

if (|input_frequency - output_frequency| <= TOLERANCE)

tests_passed += 1

}

print (tests_passed / total_tests)

    2.1.2 Enveloping

To test the enveloping functionality, we will include an envelope subtest within the Unit_Main test sketch (defined as TEST_ENV). This test will play a sample using the wavetable object, and check the amount of time (in ms) spent in each envelope state against the expected values read from the decoded sample data. Section lengths will be tested for several different MIDI notes between 0 and 127, with the goal of testing multiple samples for each instrument, as section lengths can vary between different decoded samples of a given instrument (with different note ranges). Results for each test will be displayed via the serial monitor.

Any sample instrument can be used for this test. However, tests run on samples with at least one “long” section, and/or instruments with multiple samples that have differing section lengths, are most informative. For this test, we only care about how much time the code spends in each state of the envelope, as this is the largest bug/issue we have come across and had to fix within the enveloping code.

Test Psuedocode

The following is high-level pseudocode for the basic operation of TEST_ENV.

for (each decoded sample of an instrument) {

play a note within the range of that sample

reset timer

current_state := wavetable.getEnvState()

while (wavetable.getEnvState() != STATE_IDLE) {

if (current_state != wavetable.getEnvState()) {

compare timer value with the expected section length

if (|timer - expected_length| < TOLERANCE)

tests_passed += 1

reset timer

current_state := wavetable.getEnvState()

if (current_state == STATE_SUSTAIN) {

wavetable.stop()

current_state := wavetable.getEnvState()

}

}

}

}

print (tests_passed / total_tests)

## 2.2 Performance Testing

    2.2.1 CPU Usage

To test CPU performance of the wavetable class, we will include a CPU usage subtest within Unit_Main (defined as TEST_PROC). This test will incrementally trigger more and more AudioSynthWavetable objects to play on different notes. The result will be that many different objects will eventually be playing concurrently. As each voice is added, processor usage is computed and printed to the serial monitor. Testing will stop when either the 64th voice is added or processor usage surpasses 95%. Test results will be used to determine our final benchmark numbers for the AudioSynthWavetable class.

Test Psuedocode

The following is high-level pseudocode for the basic operation of TEST_PROC.

count := 0

timer := 0 // Increments by 1 every millisecond

note := start_note

while (count < 64) {

wavetable[count].play(note);

while (timer < timer_period) {

}

proc_usage = getProcUsage()

print (proc_usage)

if (proc_usage > 95%)

break loop

else

tests_passed += 1

count += 1

note += 1

timer := 0

}

Latency

    2.2.2 Based on our research regarding perceptible audio latencies, our goal is to keep latency (time from note trigger to audio output) under 10 ms. In order to validate this, we will add a latency subtest to Unit_Main (defined as TEST_LATENCY). This test will periodically trigger playNote calls for different notes on an AudioSynthWavetable object and measure the elapsed time in ms between function call and when audio output data is detected by an AudioAnalyzePeak object. This object is only used for detecting audio output; it is not used for actual peak analysis in our context. This suffices for our purposes.

Test Psuedocode

The following is high-level pseudocode for the basic operation of TEST_LATENCY.

timer := 0 // Increments by 1 every millisecond

count := UPPER_BOUND

while (count != LOWER_BOUND) {

timer_latency := 0 // Increments by 1 every millisecond

wavetable.playNote(count)

when (peak_detector detects audio data) {

latency := timer_latency

print(latency)

if (latency ≤ TOLERANCE)

tests_passed += 1

count -= 1

}

while (timer < timer_period) {

}

timer := 0

}

## 2.3 Regression Testing

To perform regression testing, we will run the above mentioned test sketches before each major release to ensure that all of the general requirements for the system hold, including interpolation correctness, enveloping correctness, and ensuring that performance is equivalent to or better than the previous iteration. We will also add any additional “checks” to the above testing sketches upon finding specific bugs/issues that can be identified automatically.

## 2.4 System Testing

To verify that the entire system operates as expected, we utilized PyTest to generate a Python testing suite that takes in a list of various Soundfont files, and uses decoder.py to decode an instrument’s data, check that decoding passed, then automatically upload the generated files to the Teensy and ensure that compilation succeeds. This is a huge benefit in ensuring not only that our wavetable code is correct and functioning, but also that the decoder utility functions for a wide array of different Soundfonts. The Soundfont specification is quite large, and incorporates a wide portfolio of functionalities. Thus, having the ability to quickly and automatically run through a list of .sf2 files, decode them, and make sure that they compile correctly with our Wavetable class is a huge benefit and greatly increases our confidence in the system as a whole. Notes on how to run these decoder/system tests can be found in the README.md of the main repo page, as well as in the README.txt within the \DecoderTest directory of the GitHub repo.

Software Verification and Validation Plan

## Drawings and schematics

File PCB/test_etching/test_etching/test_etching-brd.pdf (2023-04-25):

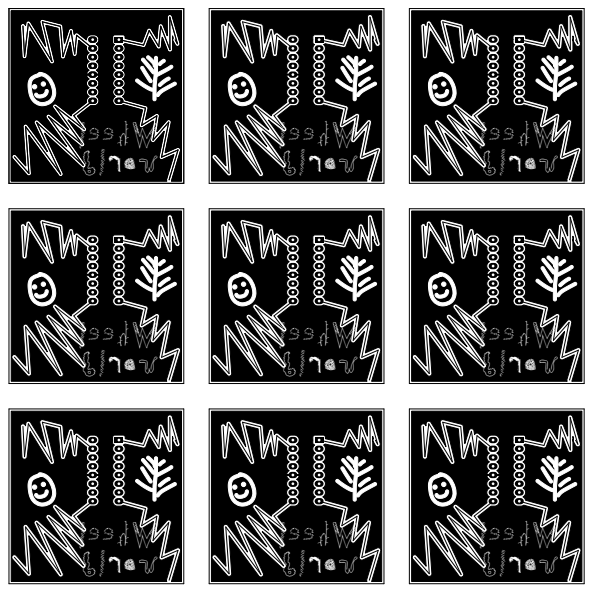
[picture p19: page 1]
Wheel world

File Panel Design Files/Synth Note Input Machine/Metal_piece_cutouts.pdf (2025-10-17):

I

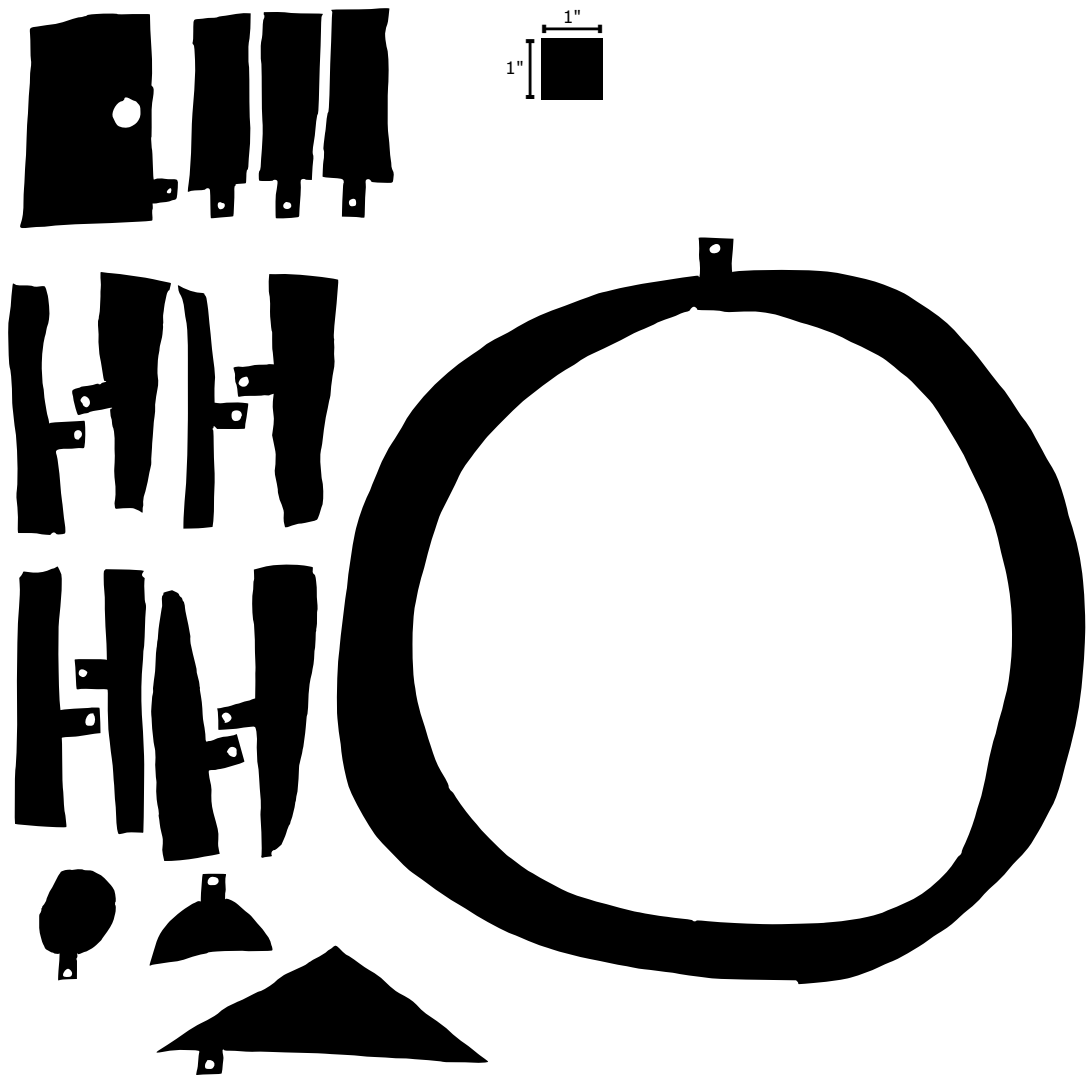
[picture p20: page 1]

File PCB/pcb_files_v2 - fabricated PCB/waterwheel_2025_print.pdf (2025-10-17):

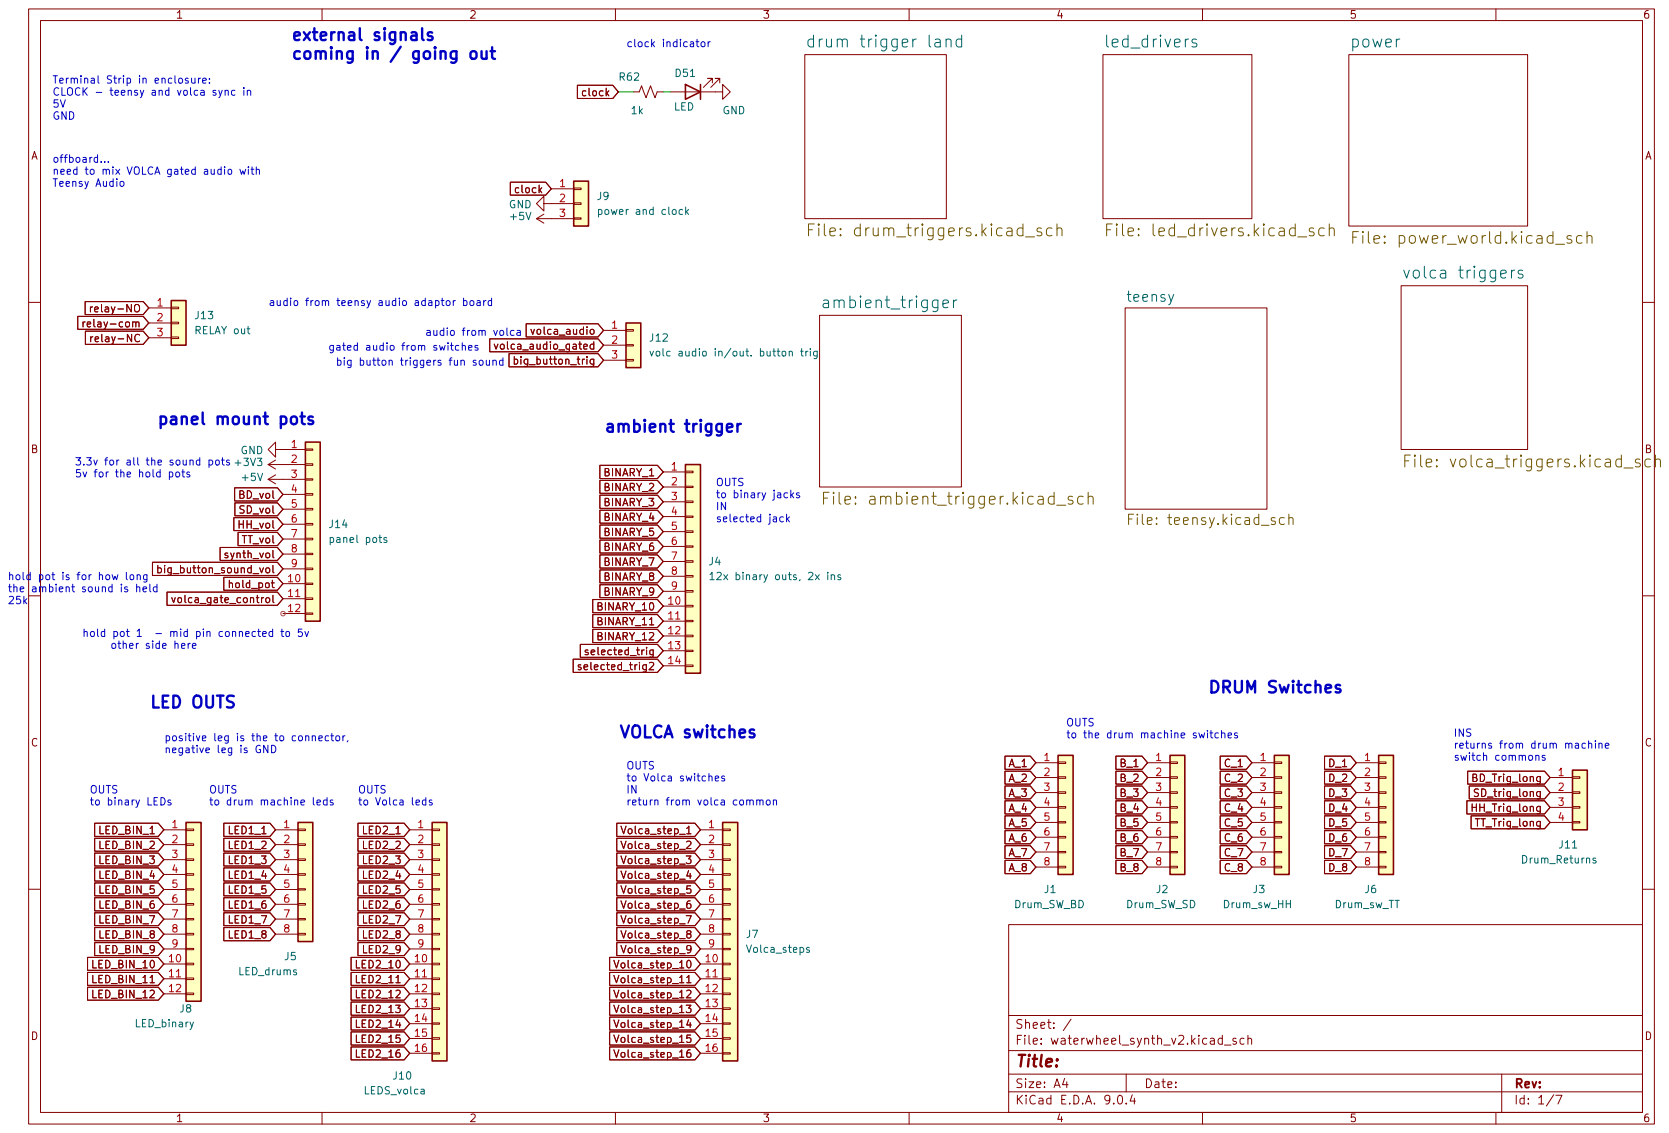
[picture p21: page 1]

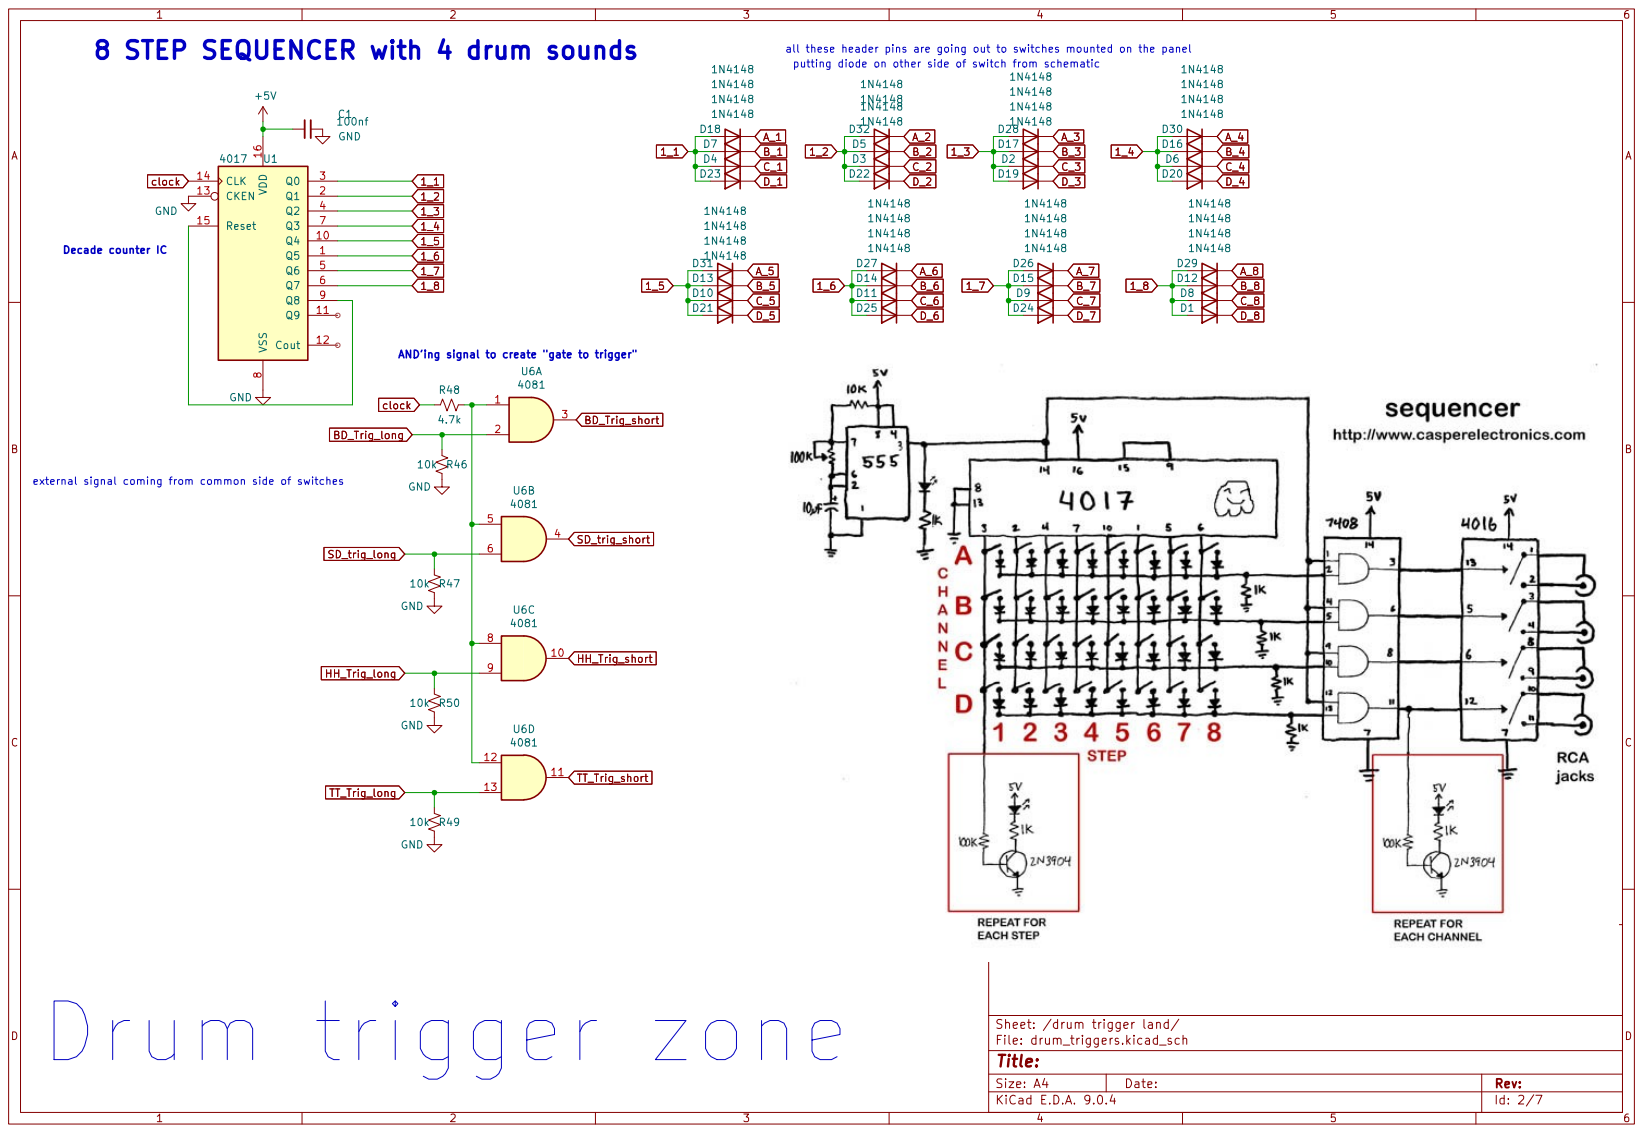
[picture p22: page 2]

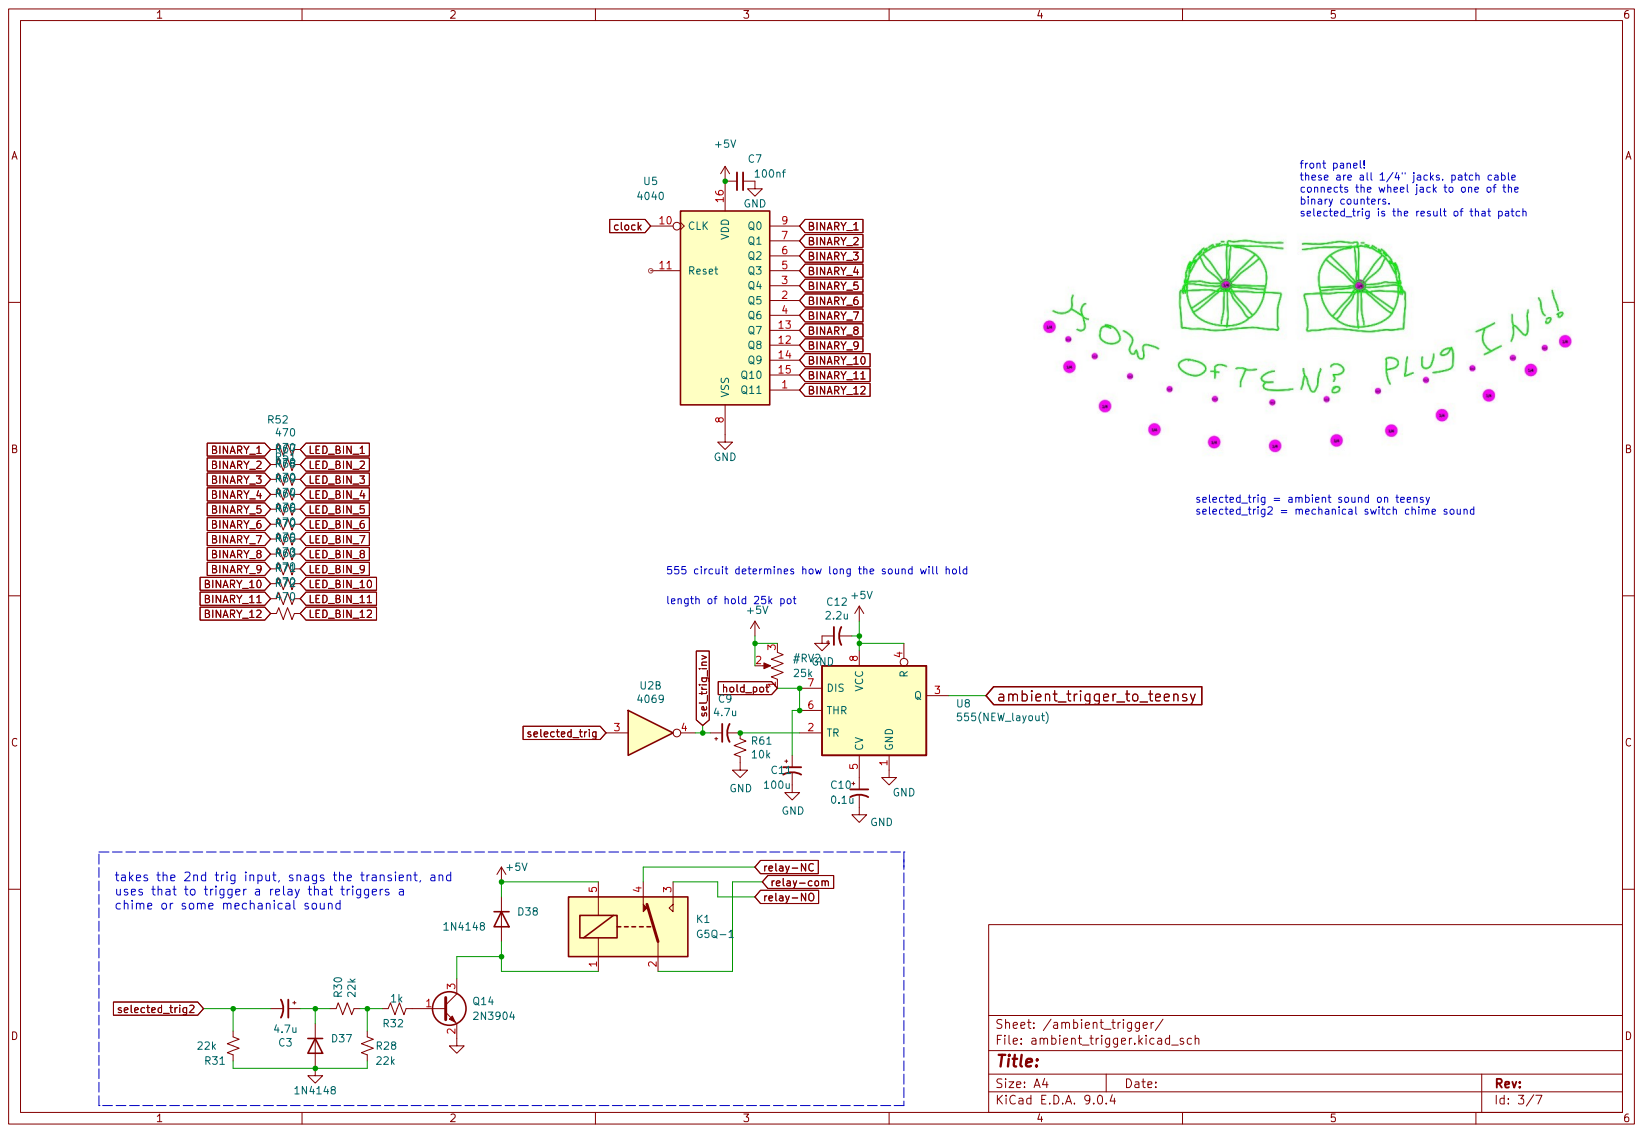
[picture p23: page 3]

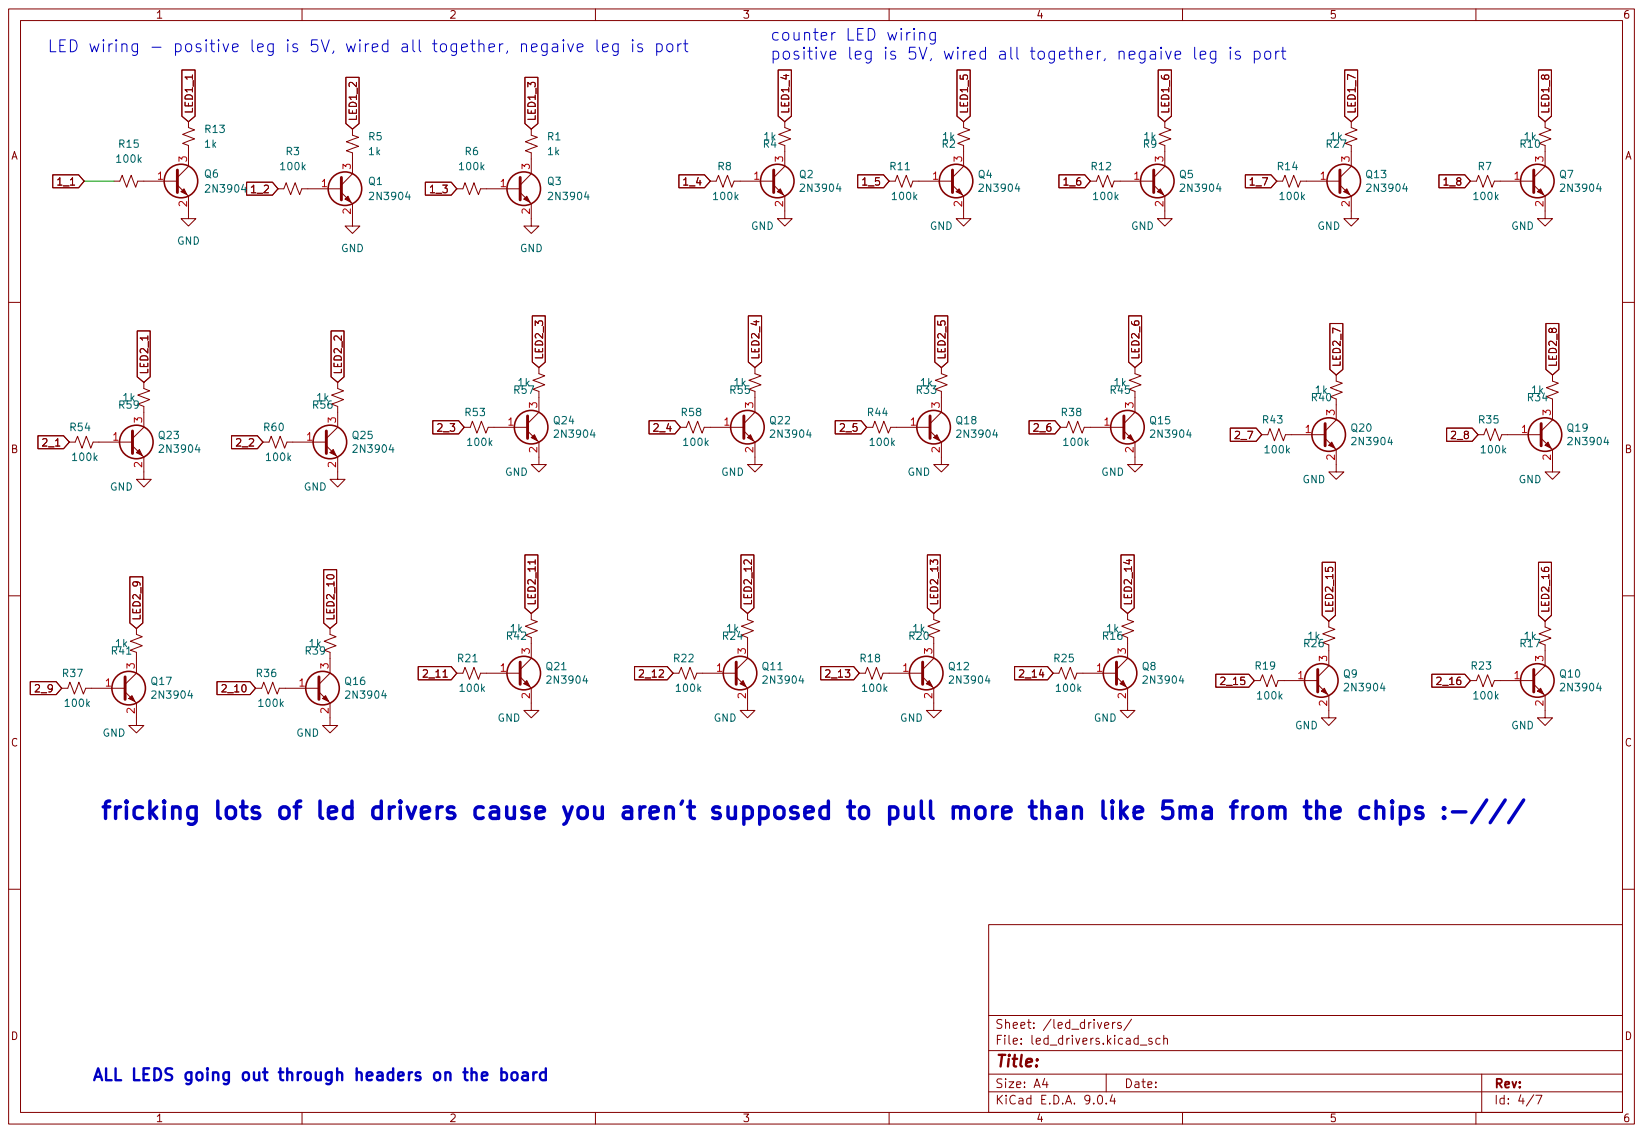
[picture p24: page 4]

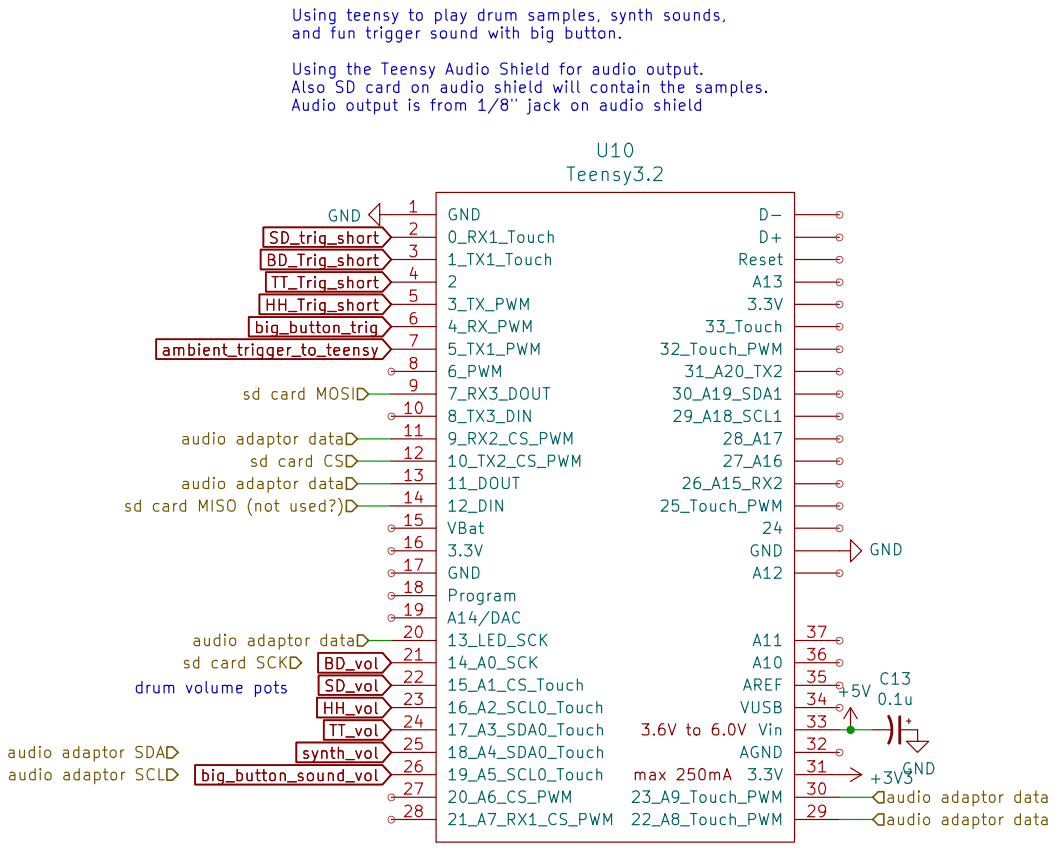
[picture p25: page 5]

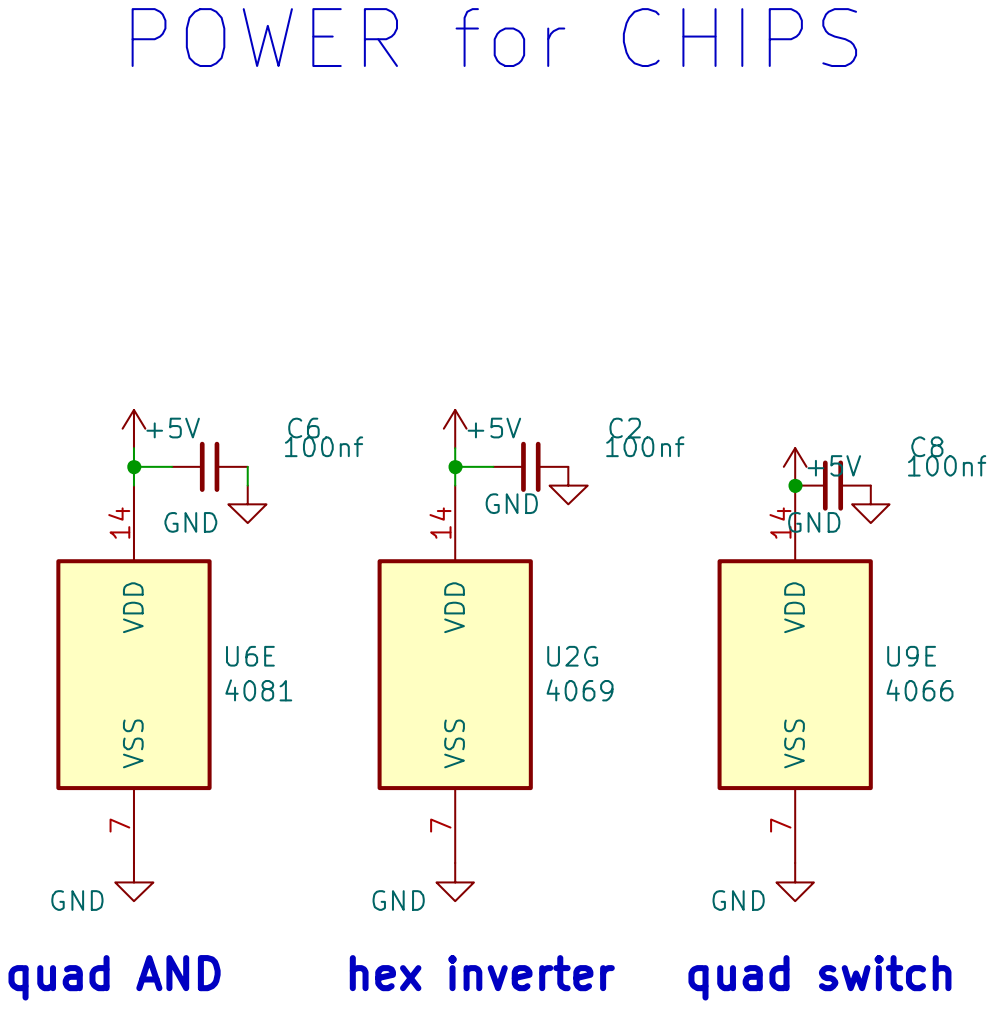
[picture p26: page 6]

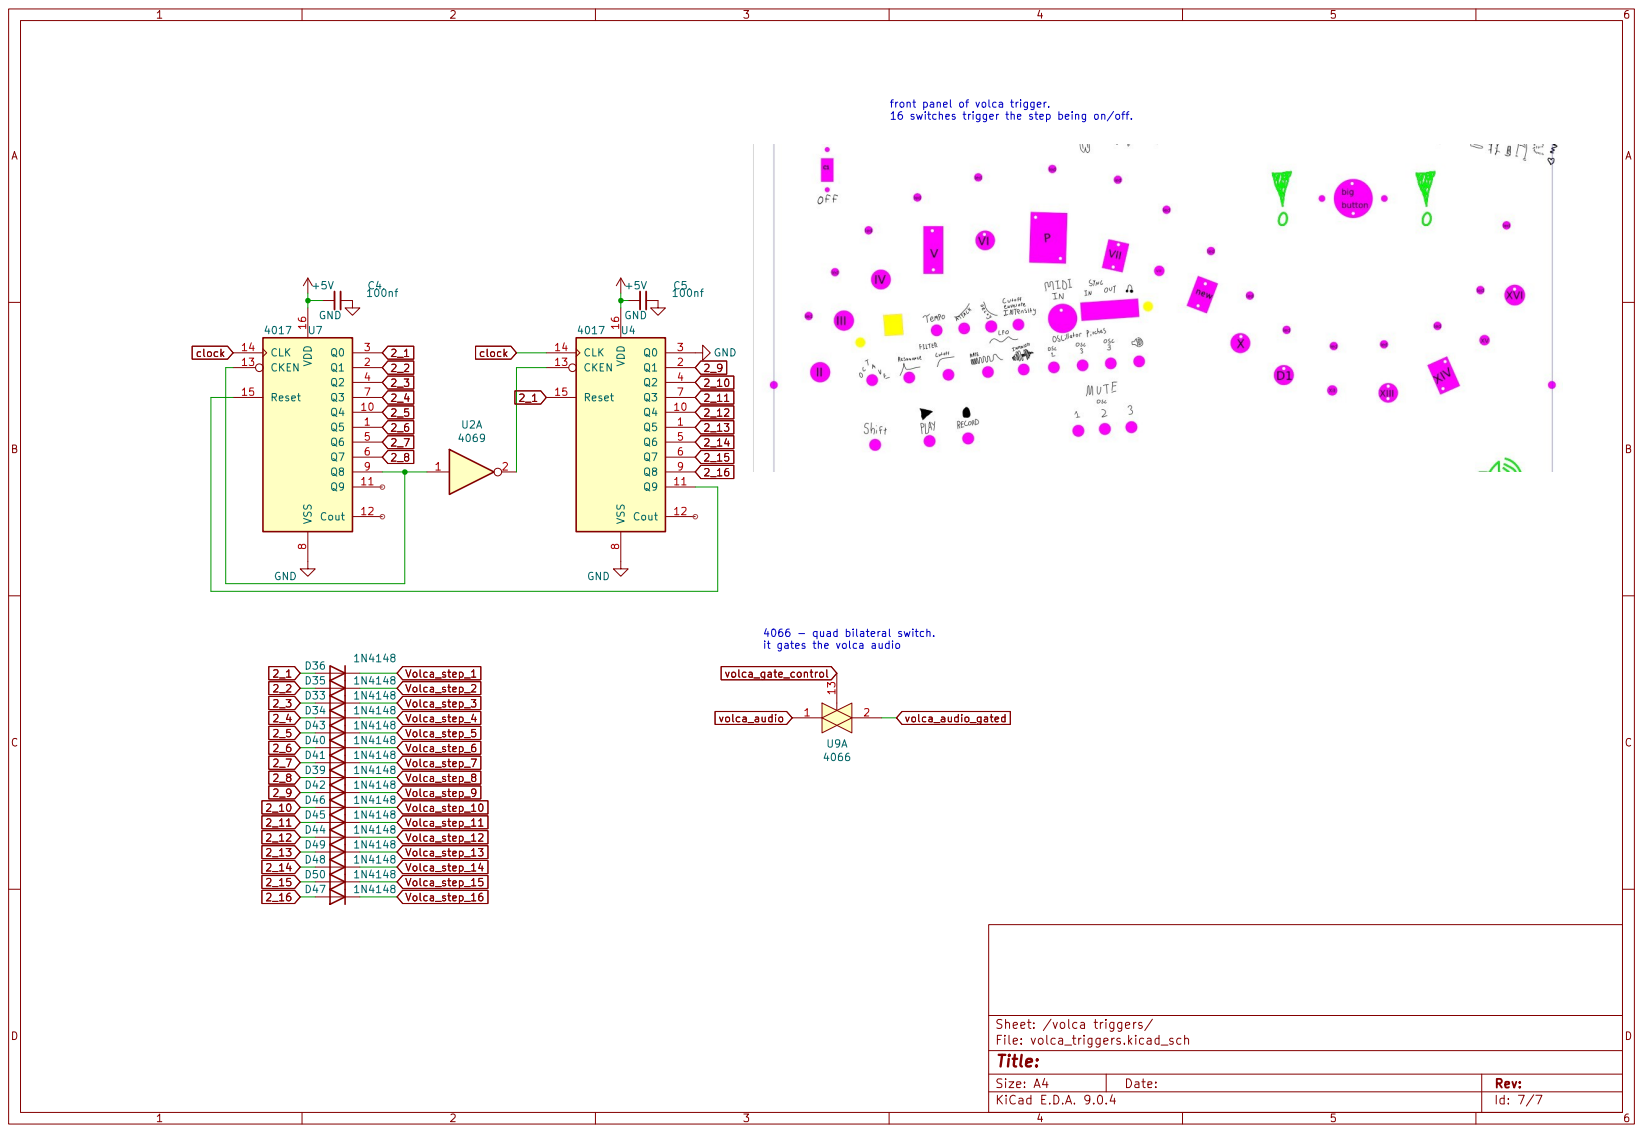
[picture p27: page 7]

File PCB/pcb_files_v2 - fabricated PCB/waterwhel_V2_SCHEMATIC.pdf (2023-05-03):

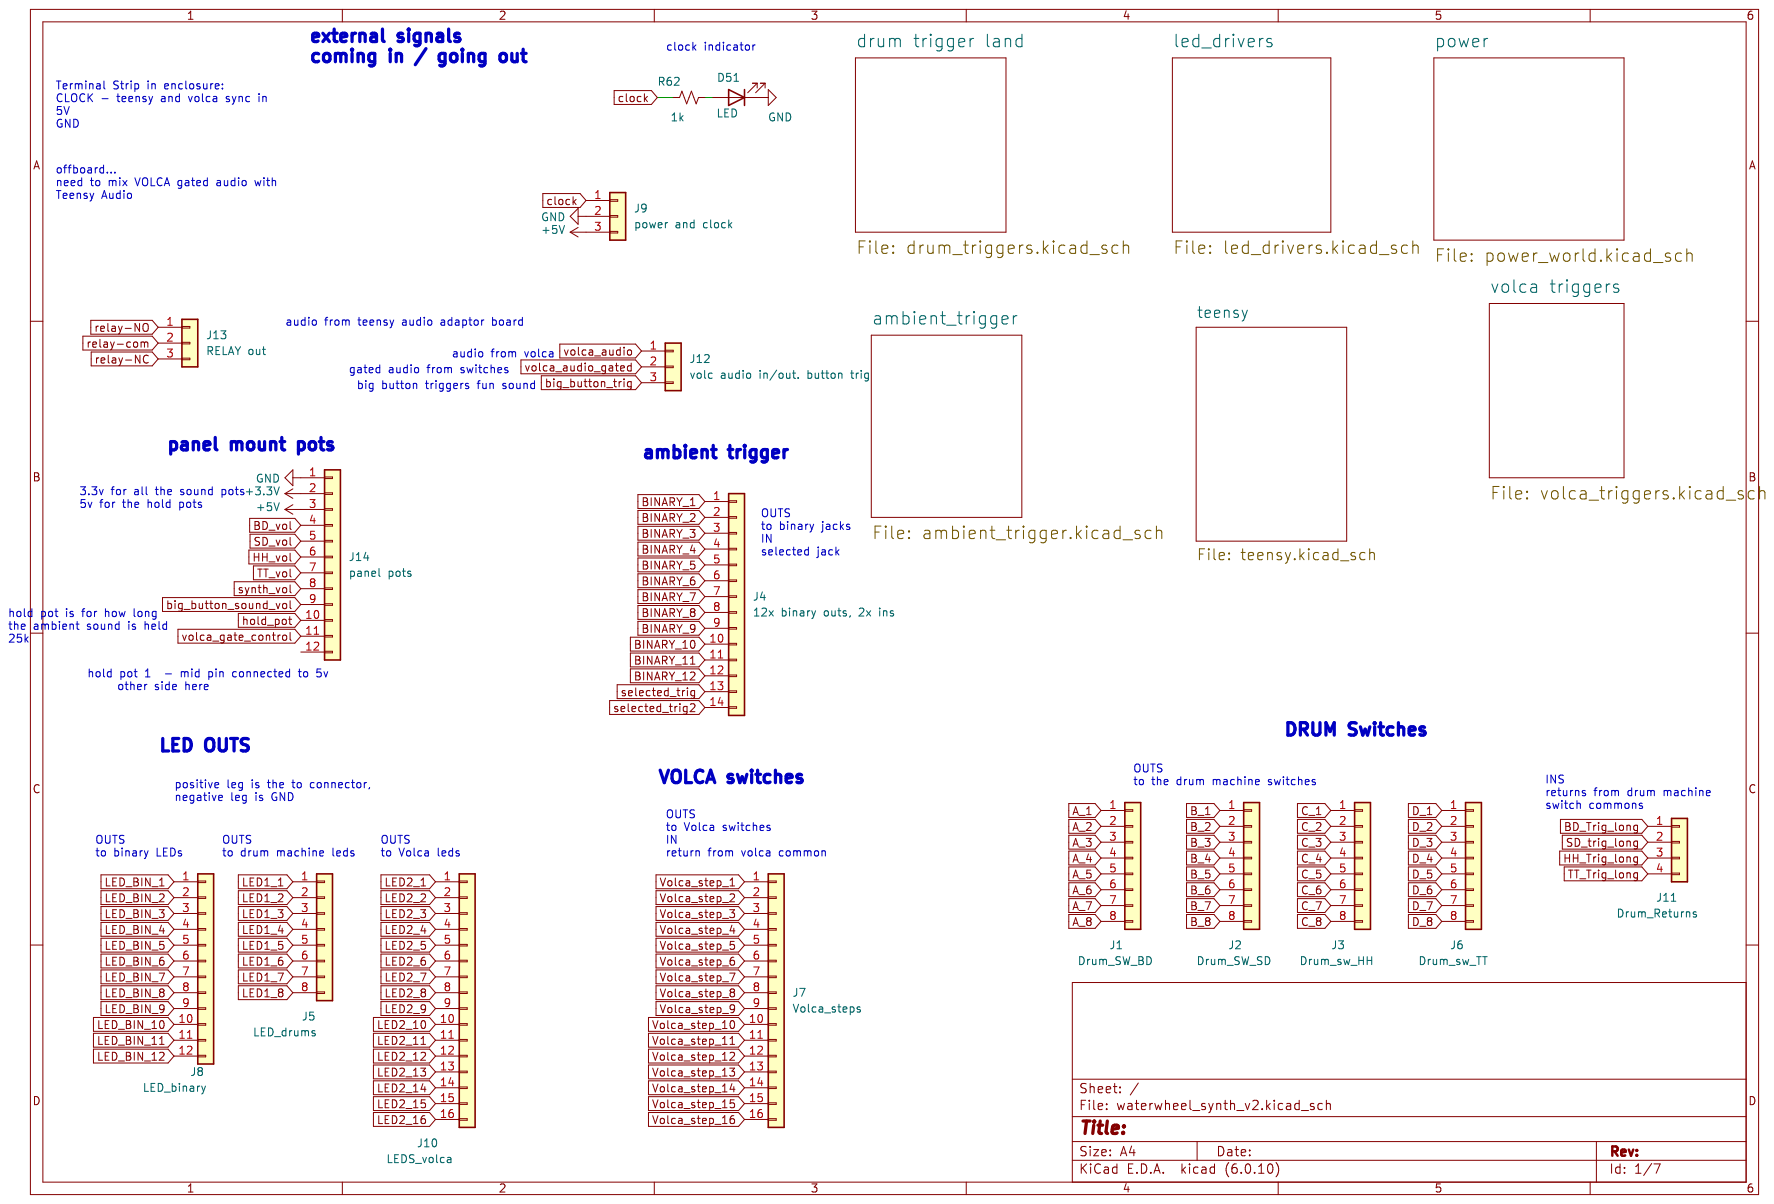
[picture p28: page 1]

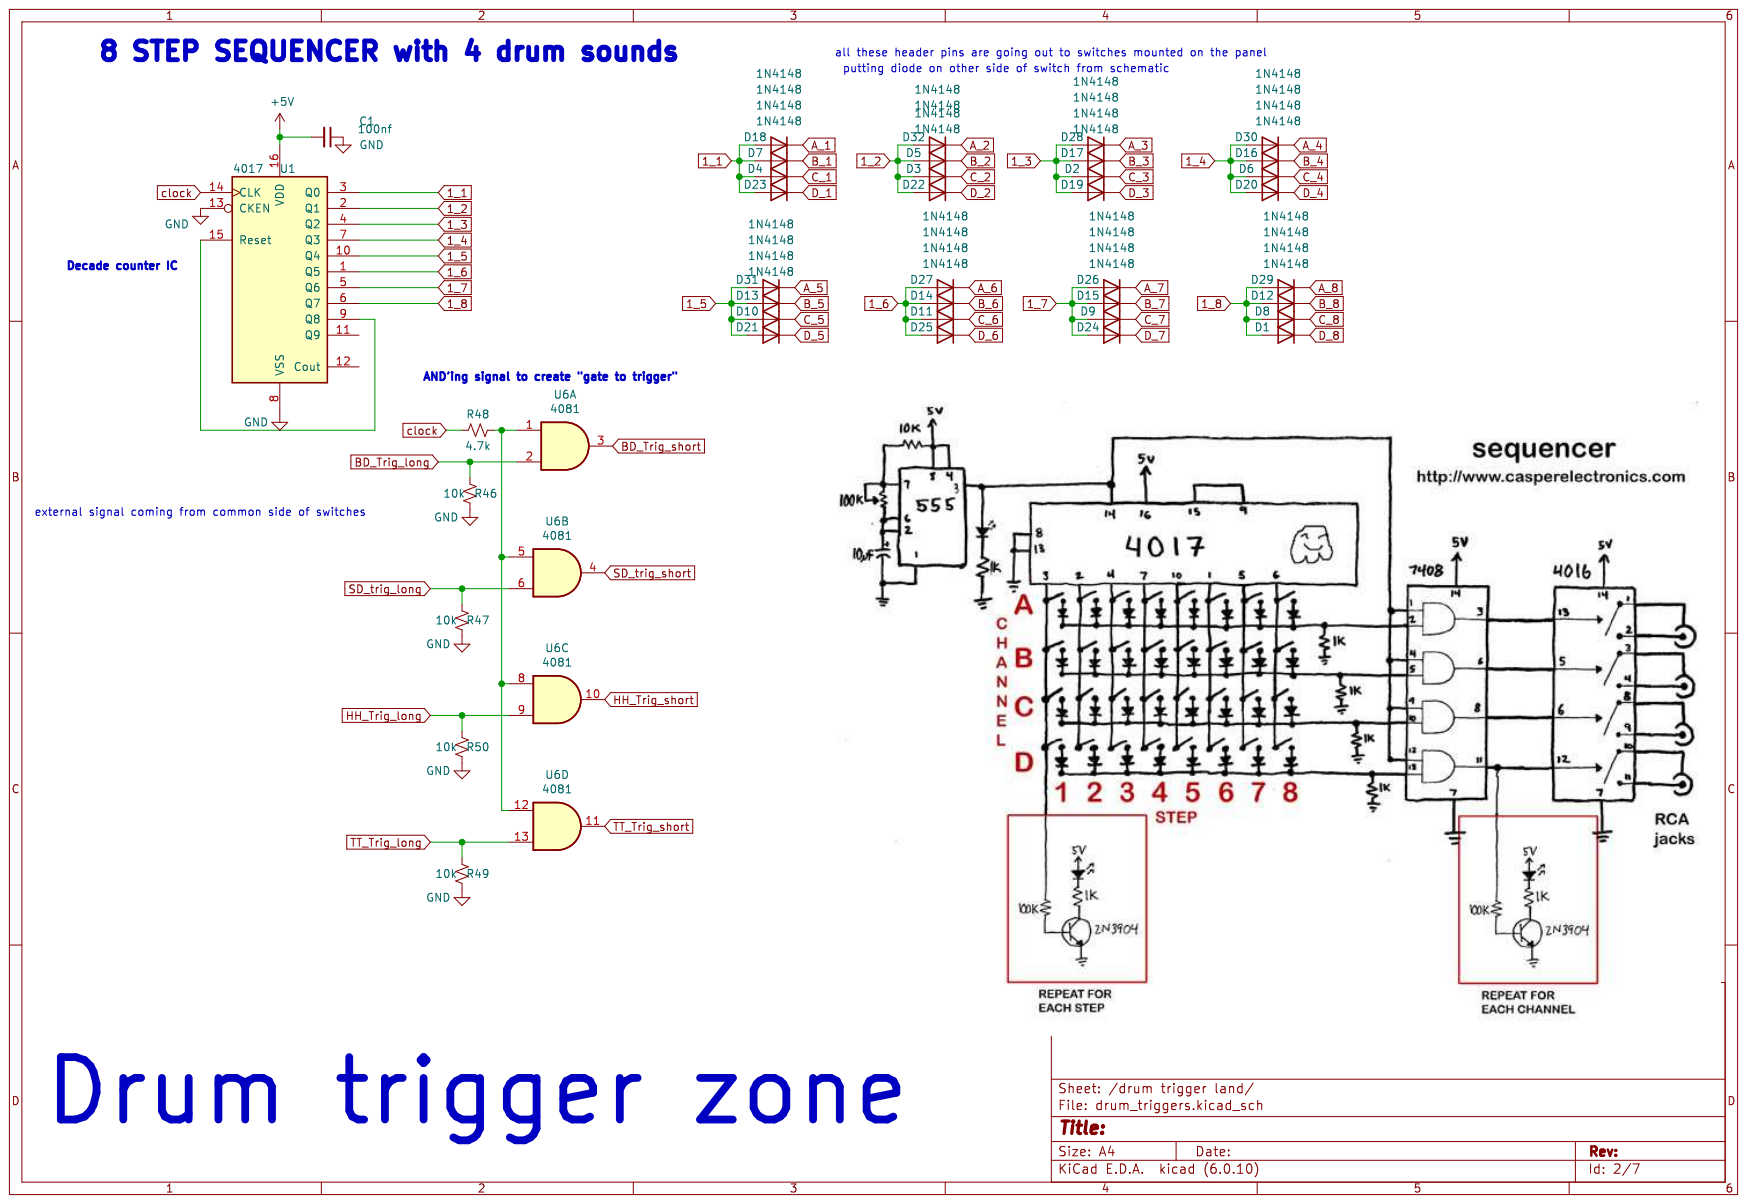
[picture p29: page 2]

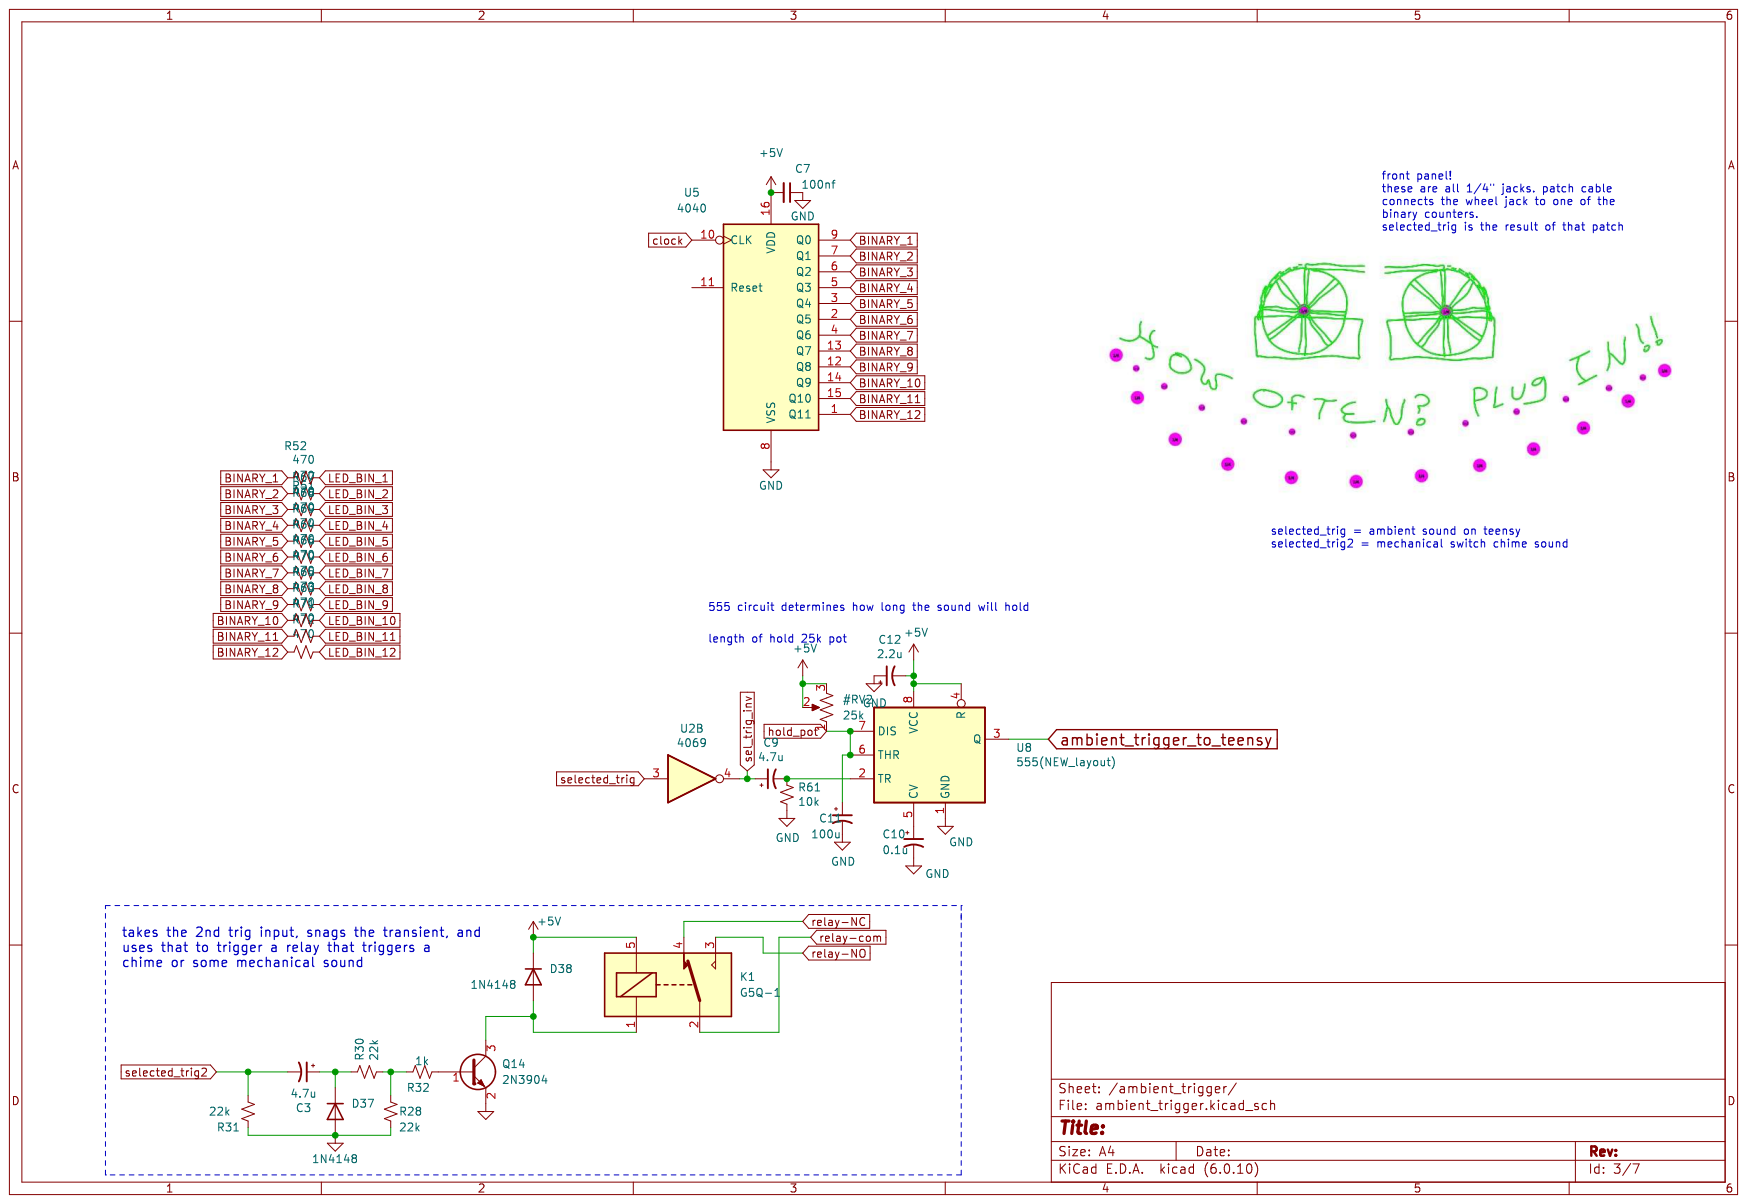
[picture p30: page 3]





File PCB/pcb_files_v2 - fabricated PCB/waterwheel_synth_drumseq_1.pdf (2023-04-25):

enchanted driveway; oct. 2022

waterwheel 8x4-drumSeq rev.1

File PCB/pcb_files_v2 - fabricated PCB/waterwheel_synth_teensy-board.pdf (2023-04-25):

leeh wreta w emi t fo; 220 2. tco

1 ve r drao b ysneet


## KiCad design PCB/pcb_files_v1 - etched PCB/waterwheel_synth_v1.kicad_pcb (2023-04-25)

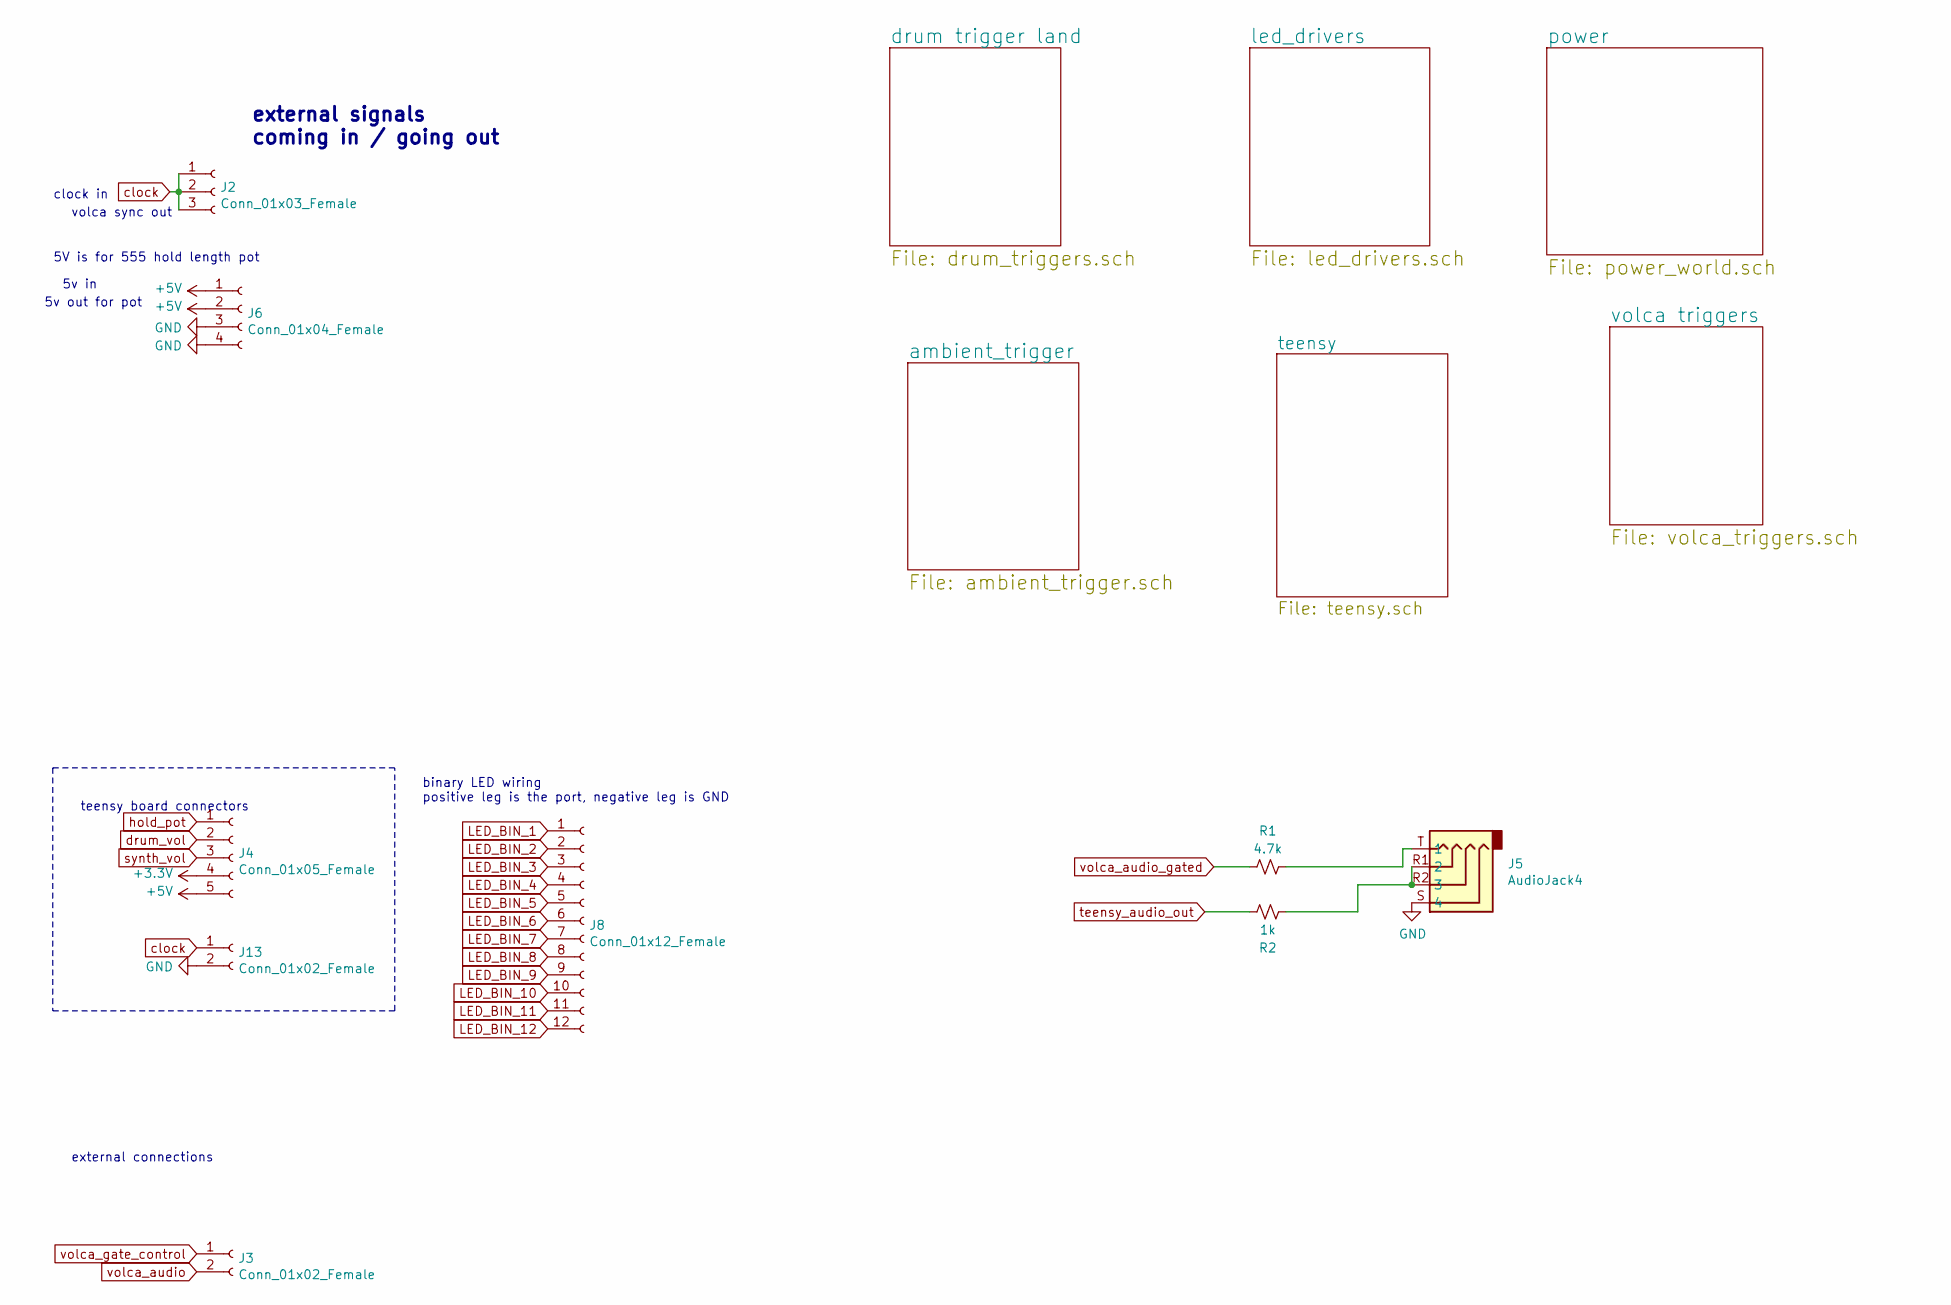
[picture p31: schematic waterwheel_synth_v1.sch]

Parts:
J2: Conn_01x03_Female; PinSocket_1x03_P2.54mm_Vertical_BIG
J3, J13: Conn_01x02_Female; PinHeader_1x02_P2.54mm_Vertical_BIG
J4: Conn_01x05_Female; PinHeader_1x05_P2.54mm_Vertical_BIG
J5: AudioJack4; sparkfun_headphone_jack
J6: Conn_01x04_Female; PinHeader_1x04_P2.54mm_Vertical_BIG
J8: Conn_01x12_Female; PinSocket_1x12_P2.54mm_Vertical_BIG
R1: 4.7k; R_Axial_DIN0207_L6.3mm_D2.5mm_P10.16mm_Horizontal_BIG
R2: 1k; R_Axial_DIN0207_L6.3mm_D2.5mm_P10.16mm_Horizontal_BIG

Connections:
+3V3: J4.4; also elsewhere on the board
+5V: J4.5, J6.1, J6.2; also elsewhere on the board
GND: J5.S (4), J6.3, J6.4, J13.2; also elsewhere on the board
LED_BIN_1: J8.1; also elsewhere on the board
LED_BIN_2: J8.2; also elsewhere on the board
LED_BIN_3: J8.3; also elsewhere on the board
LED_BIN_4: J8.4; also elsewhere on the board
LED_BIN_5: J8.5; also elsewhere on the board
LED_BIN_6: J8.6; also elsewhere on the board
LED_BIN_7: J8.7; also elsewhere on the board
LED_BIN_8: J8.8; also elsewhere on the board
LED_BIN_9: J8.9; also elsewhere on the board
LED_BIN_10: J8.10; also elsewhere on the board
LED_BIN_11: J8.11; also elsewhere on the board
LED_BIN_12: J8.12; also elsewhere on the board
unnamed: J5.R1 (2), J5.R2 (3), R2.2
unnamed: J5.T (1), R1.2
clock: J2.1, J2.2, J2.3, J13.1; also elsewhere on the board
drum_vol: J4.2; also elsewhere on the board
hold_pot: J4.1; also elsewhere on the board
synth_vol: J4.3; also elsewhere on the board
teensy_audio_out: R2.1; also elsewhere on the board
volca_audio: J3.2; also elsewhere on the board
volca_audio_gated: R1.1; also elsewhere on the board
volca_gate_control: J3.1; also elsewhere on the board

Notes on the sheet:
external signals coming in / going out
5V is for 555 hold length pot
5v out for pot
5v in
volca sync out
clock in
binary LED wiring positive leg is the port, negative leg is GND
external connections
teensy board connectors

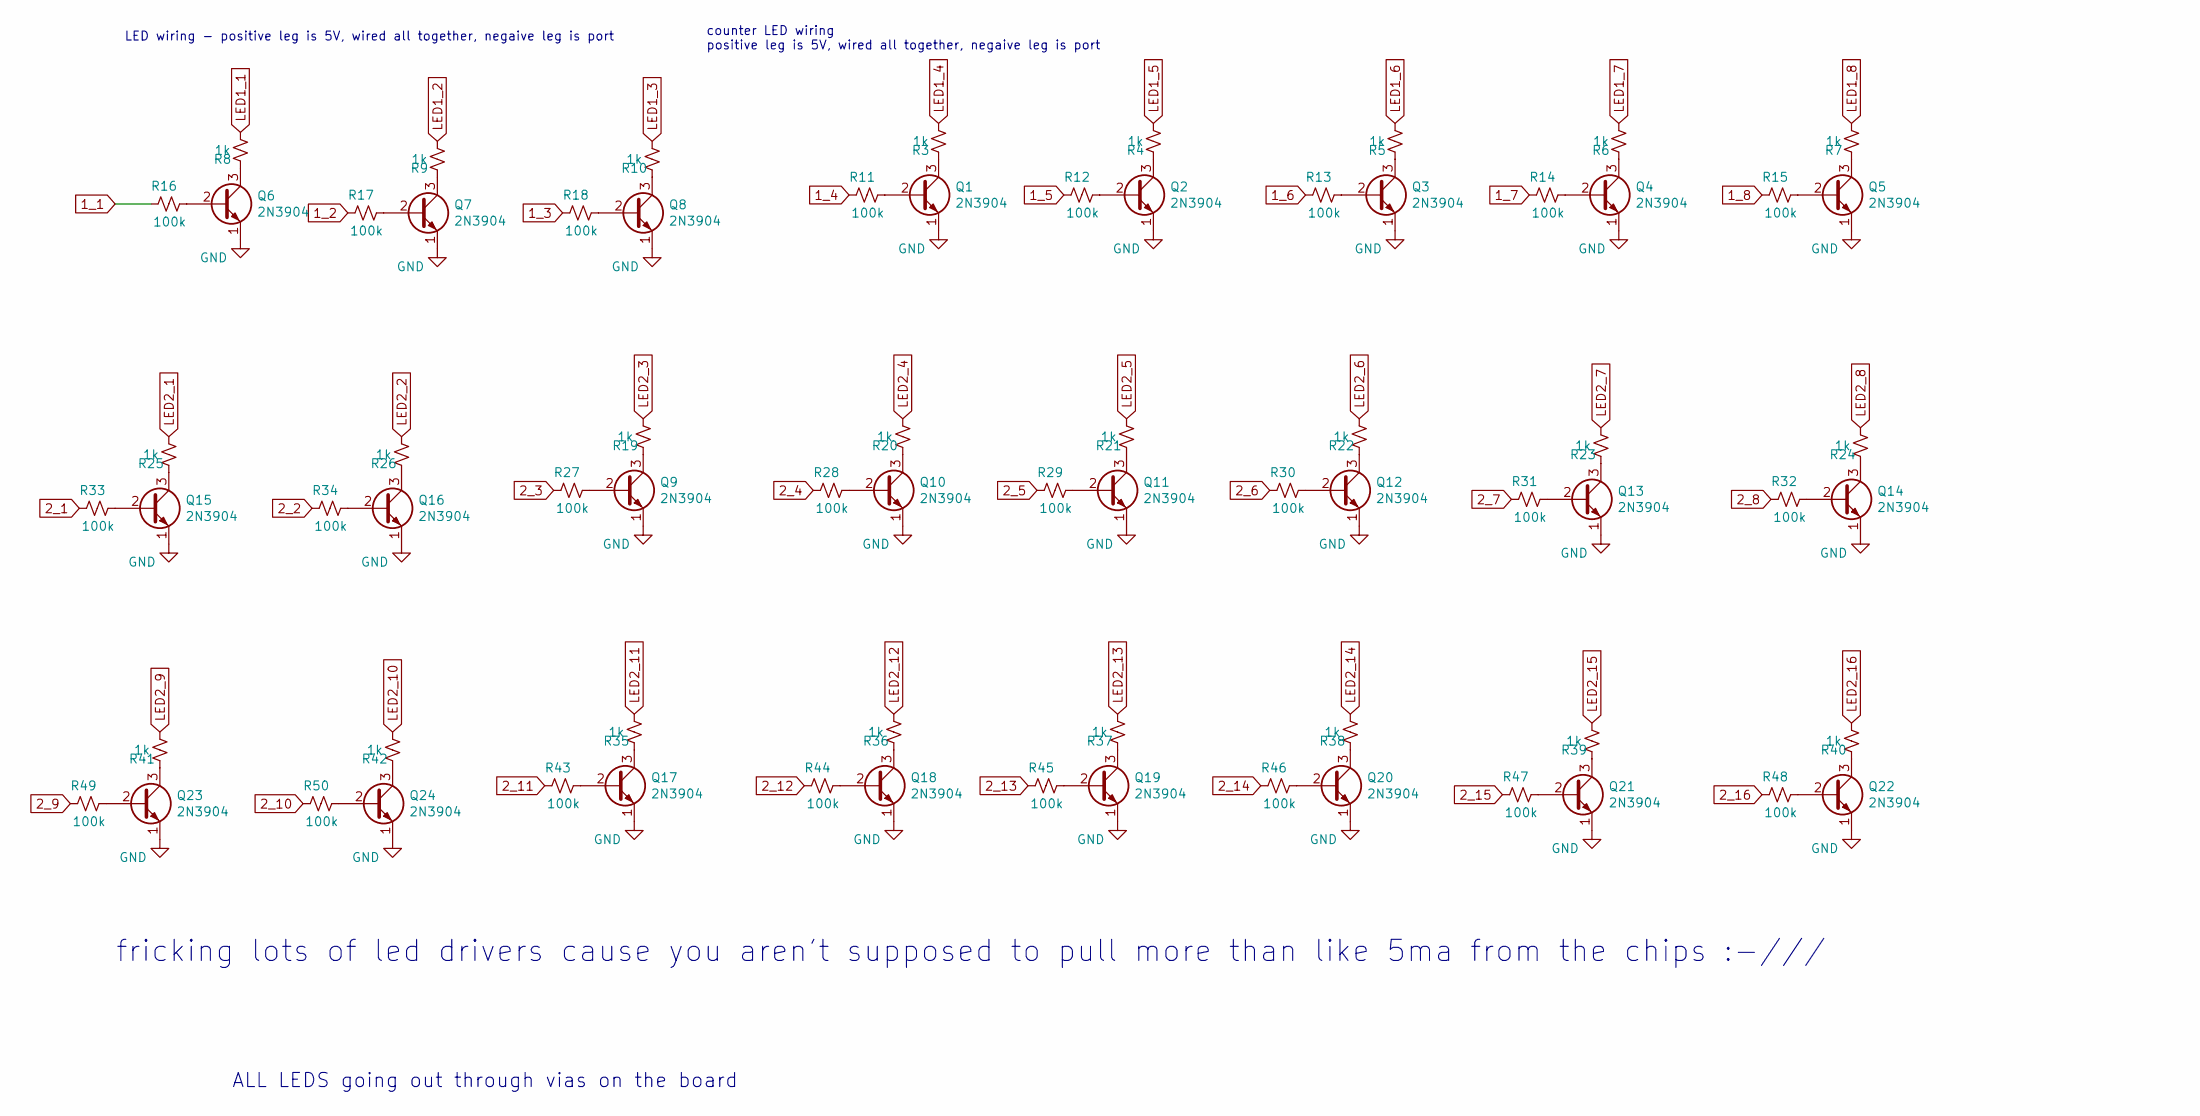
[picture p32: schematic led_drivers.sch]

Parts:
Q1, Q2, Q3, Q4, Q5, Q6, Q7, Q8, Q9, Q10, Q11, Q12, Q13, Q14, Q15, Q16, Q17, Q18, Q19, Q20, Q21, Q22, Q23, Q24: 2N3904; TO-92_Inline_Wide_BIG
R3, R4, R5, R6, R7, R8, R9, R10, R19, R20, R21, R22, R23, R24, R25, R26, R35, R36, R37, R38, R39, R40, R41, R42: 1k; R_Axial_DIN0207_L6.3mm_D2.5mm_P10.16mm_Horizontal_BIG
R11, R12, R13, R14, R15, R16, R17, R18, R27, R28, R29, R30, R31, R32, R33, R34, R43, R44, R45, R46, R47, R48, R49, R50: 100k; R_Axial_DIN0207_L6.3mm_D2.5mm_P10.16mm_Horizontal_BIG

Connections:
1_1: R16.1; also elsewhere on the board
1_2: R17.1; also elsewhere on the board
1_3: R18.1; also elsewhere on the board
1_4: R11.1; also elsewhere on the board
1_5: R12.1; also elsewhere on the board
1_6: R13.1; also elsewhere on the board
1_7: R14.1; also elsewhere on the board
1_8: R15.1; also elsewhere on the board
2_1: R33.1; also elsewhere on the board
2_2: R34.1; also elsewhere on the board
2_3: R27.1; also elsewhere on the board
2_4: R28.1; also elsewhere on the board
2_5: R29.1; also elsewhere on the board
2_6: R30.1; also elsewhere on the board
2_7: R31.1; also elsewhere on the board
2_8: R32.1; also elsewhere on the board
2_9: R49.1; also elsewhere on the board
2_10: R50.1; also elsewhere on the board
2_11: R43.1; also elsewhere on the board
2_12: R44.1; also elsewhere on the board
2_13: R45.1; also elsewhere on the board
2_14: R46.1; also elsewhere on the board
2_15: R47.1; also elsewhere on the board
2_16: R48.1; also elsewhere on the board
GND: Q1.1 (E), Q2.1 (E), Q3.1 (E), Q4.1 (E), Q5.1 (E), Q6.1 (E), Q7.1 (E), Q8.1 (E), Q9.1 (E), Q10.1 (E), Q11.1 (E), Q12.1 (E), Q13.1 (E), Q14.1 (E), Q15.1 (E), Q16.1 (E), Q17.1 (E), Q18.1 (E), Q19.1 (E), Q20.1 (E), Q21.1 (E), Q22.1 (E), Q23.1 (E), Q24.1 (E); also elsewhere on the board
LED1_1: R8.2
LED1_2: R9.2
LED1_3: R10.2
LED1_4: R3.2
LED1_5: R4.2
LED1_6: R5.2
LED1_7: R6.2
LED1_8: R7.2
LED2_1: R25.2
LED2_2: R26.2
LED2_3: R19.2
LED2_4: R20.2
LED2_5: R21.2
LED2_6: R22.2
LED2_7: R23.2
LED2_8: R24.2
LED2_9: R41.2
LED2_10: R42.2
LED2_11: R35.2
LED2_12: R36.2
LED2_13: R37.2
LED2_14: R38.2
LED2_15: R39.2
LED2_16: R40.2
unnamed: Q1.2 (B), R11.2
unnamed: Q1.3 (C), R3.1
unnamed: Q2.2 (B), R12.2
unnamed: Q2.3 (C), R4.1
unnamed: Q3.2 (B), R13.2
unnamed: Q3.3 (C), R5.1
unnamed: Q4.2 (B), R14.2
unnamed: Q4.3 (C), R6.1
unnamed: Q5.2 (B), R15.2
unnamed: Q5.3 (C), R7.1
unnamed: Q6.2 (B), R16.2
unnamed: Q6.3 (C), R8.1
unnamed: Q7.2 (B), R17.2
unnamed: Q7.3 (C), R9.1
unnamed: Q8.2 (B), R18.2
unnamed: Q8.3 (C), R10.1
unnamed: Q9.2 (B), R27.2
unnamed: Q9.3 (C), R19.1
unnamed: Q10.2 (B), R28.2
unnamed: Q10.3 (C), R20.1
unnamed: Q11.2 (B), R29.2
unnamed: Q11.3 (C), R21.1
unnamed: Q12.2 (B), R30.2
unnamed: Q12.3 (C), R22.1
unnamed: Q13.2 (B), R31.2
unnamed: Q13.3 (C), R23.1
unnamed: Q14.2 (B), R32.2
unnamed: Q14.3 (C), R24.1
unnamed: Q15.2 (B), R33.2
unnamed: Q15.3 (C), R25.1
unnamed: Q16.2 (B), R34.2
unnamed: Q16.3 (C), R26.1
unnamed: Q17.2 (B), R43.2
unnamed: Q17.3 (C), R35.1
unnamed: Q18.2 (B), R44.2
unnamed: Q18.3 (C), R36.1
unnamed: Q19.2 (B), R45.2
unnamed: Q19.3 (C), R37.1
unnamed: Q20.2 (B), R46.2
unnamed: Q20.3 (C), R38.1
unnamed: Q21.2 (B), R47.2
unnamed: Q21.3 (C), R39.1
unnamed: Q22.2 (B), R48.2
unnamed: Q22.3 (C), R40.1
unnamed: Q23.2 (B), R49.2
unnamed: Q23.3 (C), R41.1
unnamed: Q24.2 (B), R50.2
unnamed: Q24.3 (C), R42.1

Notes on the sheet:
fricking lots of led drivers cause you aren't supposed to pull more than like 5ma from the chips :-///
LED wiring - positive leg is 5V, wired all together, negaive leg is port
counter LED wiring positive leg is 5V, wired all together, negaive leg is port
ALL LEDS going out through vias on the board

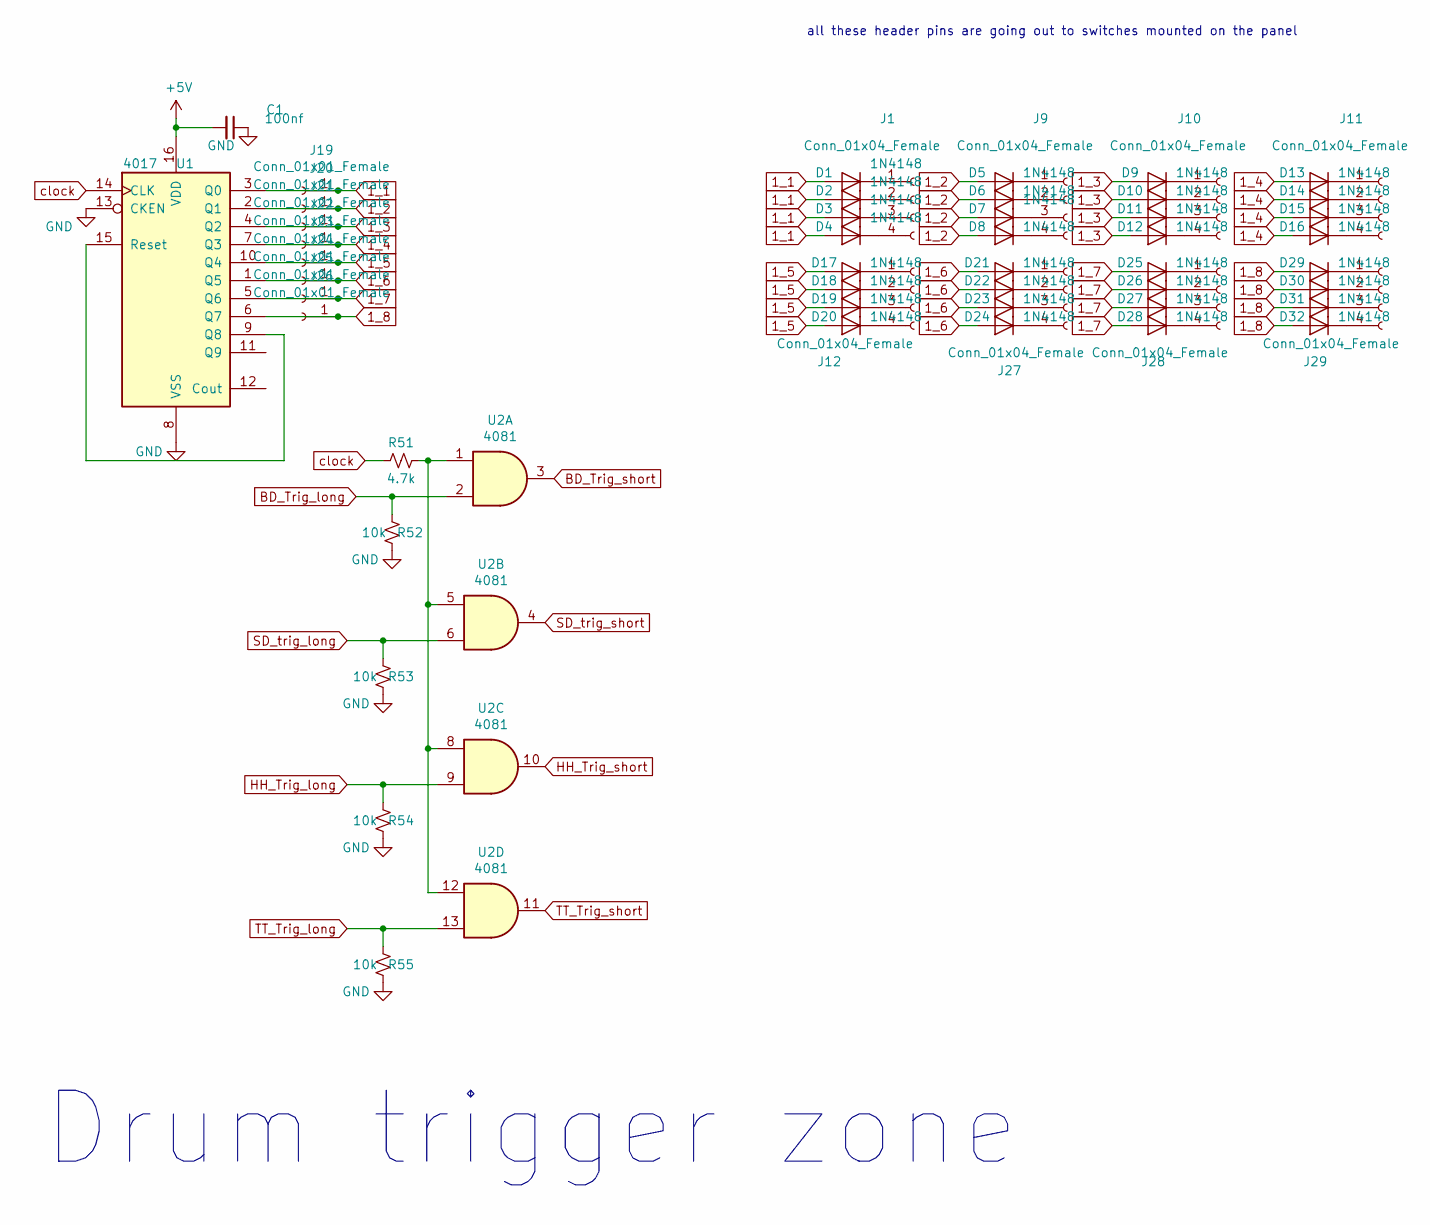
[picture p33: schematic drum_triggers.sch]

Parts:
C1: 100nf; C_Axial_L3.8mm_D2.6mm_P7.50mm_Horizontal_BIG
D1, D2, D3, D4, D5, D6, D7, D8, D9, D10, D11, D12, D13, D14, D15, D16, D17, D18, D19, D20, D21, D22, D23, D24, D25, D26, D27, D28, D29, D30, D31, D32: 1N4148; D_DO-35_SOD27_P7.62mm_Horizontal_BIG
J1, J9, J10, J11, J12, J27, J28, J29: Conn_01x04_Female; PinHeader_1x04_P2.54mm_Vertical_BIG
J19, J20, J21, J22, J23, J24, J25, J26: Conn_01x01_Female; PinHeader_1x01_P2.54mm_Vertical_BIG
R51: 4.7k; R_Axial_DIN0207_L6.3mm_D2.5mm_P10.16mm_Horizontal_BIG
R52, R53, R54, R55: 10k; R_Axial_DIN0207_L6.3mm_D2.5mm_P10.16mm_Horizontal_BIG
U1: 4017; DIP-16_W7.62mm_Socket_LongPads
U2: 4081; DIP-14_W7.62mm_Socket_LongPads

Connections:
1_1: D1.2 (A), D2.2 (A), D3.2 (A), D4.2 (A), J19.1, U1.3 (Q0); also elsewhere on the board
1_2: D5.2 (A), D6.2 (A), D7.2 (A), D8.2 (A), J20.1, U1.2 (Q1); also elsewhere on the board
1_3: D9.2 (A), D10.2 (A), D11.2 (A), D12.2 (A), J21.1, U1.4 (Q2); also elsewhere on the board
1_4: D13.2 (A), D14.2 (A), D15.2 (A), D16.2 (A), J22.1, U1.7 (Q3); also elsewhere on the board
1_5: D17.2 (A), D18.2 (A), D19.2 (A), D20.2 (A), J23.1, U1.10 (Q4); also elsewhere on the board
1_6: D21.2 (A), D22.2 (A), D23.2 (A), D24.2 (A), J24.1, U1.1 (Q5); also elsewhere on the board
1_7: D25.2 (A), D26.2 (A), D27.2 (A), D28.2 (A), J25.1, U1.5 (Q6); also elsewhere on the board
1_8: D29.2 (A), D30.2 (A), D31.2 (A), D32.2 (A), J26.1, U1.6 (Q7); also elsewhere on the board
+5V: C1.2, U1.16 (VDD); also elsewhere on the board
BD_Trig_long: R52.2, U2.2
BD_Trig_short: U2.3; also elsewhere on the board
GND: C1.1, R52.1, R53.1, R54.1, R55.1, U1.8 (VSS), U1.13 (CKEN); also elsewhere on the board
HH_Trig_long: R54.2, U2.9
HH_Trig_short: U2.10; also elsewhere on the board
unnamed: D1.1 (K), J1.1
unnamed: D2.1 (K), J1.2
unnamed: D3.1 (K), J1.3
unnamed: D4.1 (K), J1.4
unnamed: D5.1 (K), J9.1
unnamed: D6.1 (K), J9.2
unnamed: D7.1 (K), J9.3
unnamed: D8.1 (K), J9.4
unnamed: D9.1 (K), J10.1
unnamed: D10.1 (K), J10.2
unnamed: D11.1 (K), J10.3
unnamed: D12.1 (K), J10.4
unnamed: D13.1 (K), J11.1
unnamed: D14.1 (K), J11.2
unnamed: D15.1 (K), J11.3
unnamed: D16.1 (K), J11.4
unnamed: D17.1 (K), J12.1
unnamed: D18.1 (K), J12.2
unnamed: D19.1 (K), J12.3
unnamed: D20.1 (K), J12.4
unnamed: D21.1 (K), J27.1
unnamed: D22.1 (K), J27.2
unnamed: D23.1 (K), J27.3
unnamed: D24.1 (K), J27.4
unnamed: D25.1 (K), J28.1
unnamed: D26.1 (K), J28.2
unnamed: D27.1 (K), J28.3
unnamed: D28.1 (K), J28.4
unnamed: D29.1 (K), J29.1
unnamed: D30.1 (K), J29.2
unnamed: D31.1 (K), J29.3
unnamed: D32.1 (K), J29.4
unnamed: R51.1, U2.1, U2.5, U2.8, U2.12
unnamed: U1.9 (Q8), U1.15 (Reset)
SD_trig_long: R53.2, U2.6
SD_trig_short: U2.4; also elsewhere on the board
TT_Trig_long: R55.2, U2.13
TT_Trig_short: U2.11; also elsewhere on the board
clock: R51.2, U1.14 (CLK); also elsewhere on the board

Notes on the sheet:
Drum trigger zone
all these header pins are going out to switches mounted on the panel

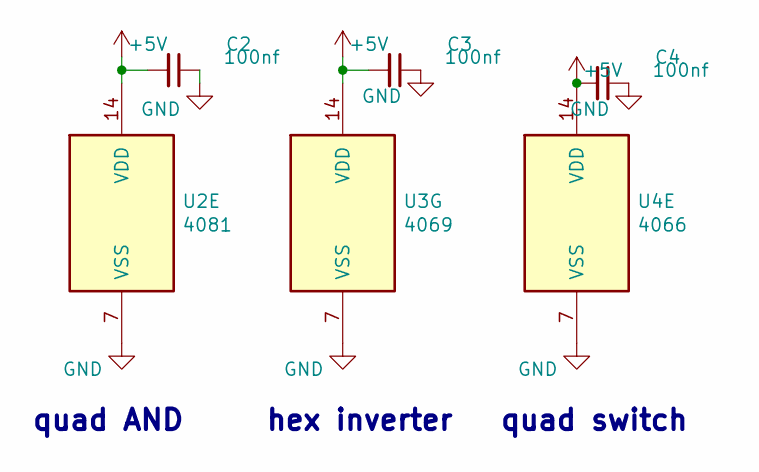
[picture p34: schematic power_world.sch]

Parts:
C2, C3, C4: 100nf; C_Axial_L3.8mm_D2.6mm_P7.50mm_Horizontal_BIG
U2: 4081; DIP-14_W7.62mm_Socket_LongPads
U3: 4069; DIP-14_W7.62mm_Socket_LongPads
U4: 4066; DIP-14_W7.62mm_Socket_LongPads

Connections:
+5V: C2.2, C3.2, C4.2, U2.14 (VDD), U3.14 (VDD), U4.14 (VDD); also elsewhere on the board
GND: C2.1, C3.1, C4.1, U2.7 (VSS), U3.7 (VSS), U4.7 (VSS); also elsewhere on the board

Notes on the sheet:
hex inverter
quad AND
quad switch

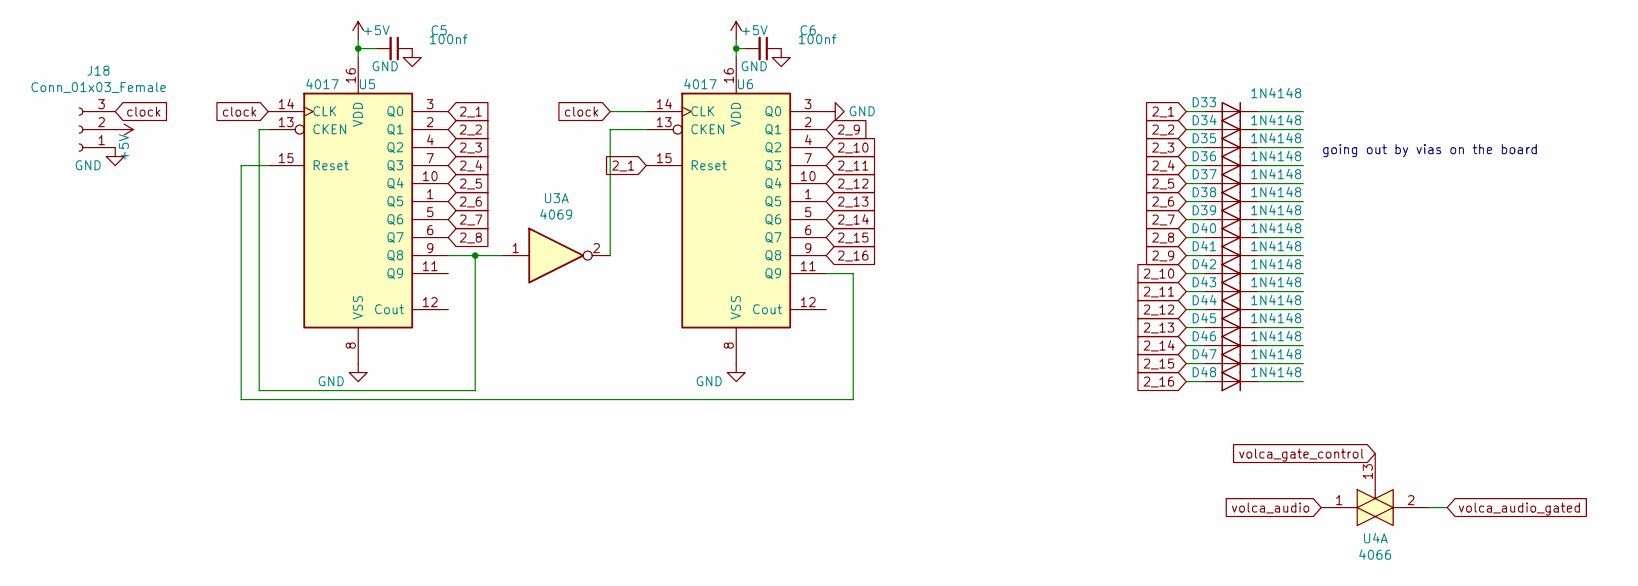
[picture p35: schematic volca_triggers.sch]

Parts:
C5, C6: 100nf; C_Axial_L3.8mm_D2.6mm_P7.50mm_Horizontal_BIG
D33, D34, D35, D36, D37, D38, D39, D40, D41, D42, D43, D44, D45, D46, D47, D48: 1N4148; D_DO-35_SOD27_P7.62mm_Horizontal_BIG
J18: Conn_01x03_Female; PinSocket_1x03_P2.54mm_Vertical_BIG
U3: 4069; DIP-14_W7.62mm_Socket_LongPads
U4: 4066; DIP-14_W7.62mm_Socket_LongPads
U5, U6: 4017; DIP-16_W7.62mm_Socket_LongPads

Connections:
2_1: D33.2 (A), U5.3 (Q0), U6.15 (Reset); also elsewhere on the board
2_2: D34.2 (A), U5.2 (Q1); also elsewhere on the board
2_3: D35.2 (A), U5.4 (Q2); also elsewhere on the board
2_4: D36.2 (A), U5.7 (Q3); also elsewhere on the board
2_5: D37.2 (A), U5.10 (Q4); also elsewhere on the board
2_6: D38.2 (A), U5.1 (Q5); also elsewhere on the board
2_7: D39.2 (A), U5.5 (Q6); also elsewhere on the board
2_8: D40.2 (A), U5.6 (Q7); also elsewhere on the board
2_9: D41.2 (A), U6.2 (Q1); also elsewhere on the board
2_10: D42.2 (A), U6.4 (Q2); also elsewhere on the board
2_11: D43.2 (A), U6.7 (Q3); also elsewhere on the board
2_12: D44.2 (A), U6.10 (Q4); also elsewhere on the board
2_13: D45.2 (A), U6.1 (Q5); also elsewhere on the board
2_14: D46.2 (A), U6.5 (Q6); also elsewhere on the board
2_15: D47.2 (A), U6.6 (Q7); also elsewhere on the board
2_16: D48.2 (A), U6.9 (Q8); also elsewhere on the board
+5V: C5.2, C6.2, J18.2, U5.16 (VDD), U6.16 (VDD); also elsewhere on the board
GND: C5.1, C6.1, J18.1, U5.8 (VSS), U6.3 (Q0), U6.8 (VSS); also elsewhere on the board
unnamed: U3.1, U5.9 (Q8), U5.13 (CKEN)
unnamed: U3.2, U6.13 (CKEN)
unnamed: U5.15 (Reset), U6.11 (Q9)
clock: J18.3, U5.14 (CLK), U6.14 (CLK); also elsewhere on the board
volca_audio: U4.1; also elsewhere on the board
volca_audio_gated: U4.2; also elsewhere on the board
volca_gate_control: U4.13; also elsewhere on the board

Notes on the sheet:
going out by vias on the board

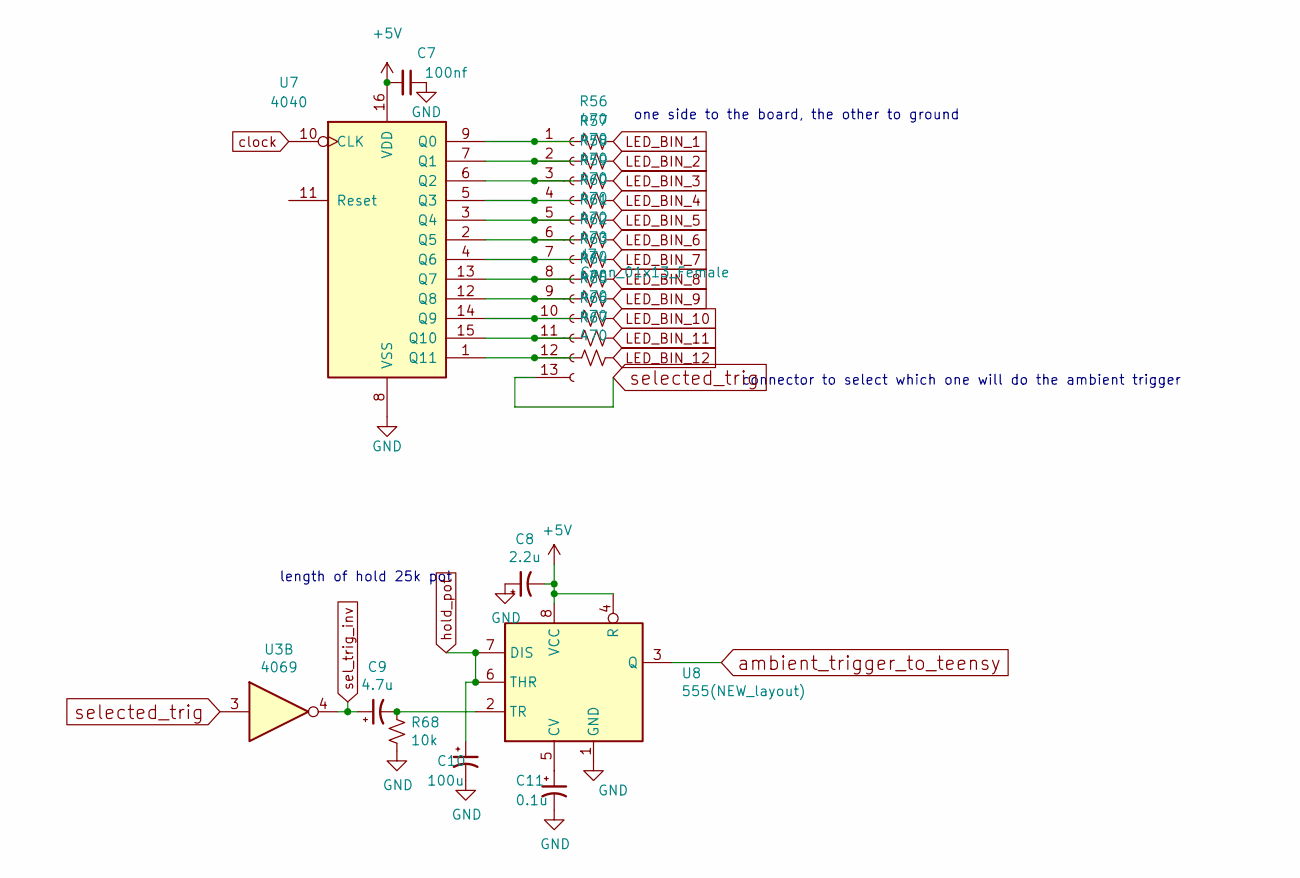
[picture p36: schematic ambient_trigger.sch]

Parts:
C7: 100nf; C_Axial_L3.8mm_D2.6mm_P7.50mm_Horizontal_BIG
C8: 2.2u; C_Axial_L3.8mm_D2.6mm_P7.50mm_Horizontal_BIG
C9: 4.7u; C_Axial_L3.8mm_D2.6mm_P7.50mm_Horizontal_BIG
C10: 100u; C_Axial_L3.8mm_D2.6mm_P7.50mm_Horizontal_BIG
C11: 0.1u; C_Axial_L3.8mm_D2.6mm_P7.50mm_Horizontal_BIG
J7: Conn_01x13_Female; PinHeader_1x13_P2.54mm_Vertical_BIG
R56, R57, R58, R59, R60, R61, R62, R63, R64, R65, R66, R67: 470; R_Axial_DIN0207_L6.3mm_D2.5mm_P10.16mm_Horizontal_BIG
R68: 10k; R_Axial_DIN0207_L6.3mm_D2.5mm_P10.16mm_Horizontal_BIG
U3: 4069; DIP-14_W7.62mm_Socket_LongPads
U7: 4040; DIP-16_W7.62mm_Socket_LongPads
U8: 555(NEW_layout); DIP-8_W7.62mm_Socket_LongPads

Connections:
+5V: C7.2, C8.2, U7.16 (VDD), U8.4 (R), U8.8 (VCC); also elsewhere on the board
GND: C7.1, C8.1, C10.2, C11.2, R68.1, U7.8 (VSS), U8.1 (GND); also elsewhere on the board
LED_BIN_1: R56.1; also elsewhere on the board
LED_BIN_2: R57.1; also elsewhere on the board
LED_BIN_3: R58.1; also elsewhere on the board
LED_BIN_4: R59.1; also elsewhere on the board
LED_BIN_5: R60.1; also elsewhere on the board
LED_BIN_6: R61.1; also elsewhere on the board
LED_BIN_7: R62.1; also elsewhere on the board
LED_BIN_8: R63.1; also elsewhere on the board
LED_BIN_9: R64.1; also elsewhere on the board
LED_BIN_10: R65.1; also elsewhere on the board
LED_BIN_11: R66.1; also elsewhere on the board
LED_BIN_12: R67.1; also elsewhere on the board
unnamed: C9.2, R68.2, U8.2 (TR)
unnamed: C11.1, U8.5 (CV)
unnamed: J7.1, R56.2, U7.9 (Q0)
unnamed: J7.2, R57.2, U7.7 (Q1)
unnamed: J7.3, R58.2, U7.6 (Q2)
unnamed: J7.4, R59.2, U7.5 (Q3)
unnamed: J7.5, R60.2, U7.3 (Q4)
unnamed: J7.6, R61.2, U7.2 (Q5)
unnamed: J7.7, R62.2, U7.4 (Q6)
unnamed: J7.8, R63.2, U7.13 (Q7)
unnamed: J7.9, R64.2, U7.12 (Q8)
unnamed: J7.10, R65.2, U7.14 (Q9)
unnamed: J7.11, R66.2, U7.15 (Q10)
unnamed: J7.12, R67.2, U7.1 (Q11)
ambient_trigger_to_teensy: U8.3 (Q); also elsewhere on the board
clock: U7.10 (CLK); also elsewhere on the board
hold_pot: C10.1, U8.6 (THR), U8.7 (DIS); also elsewhere on the board
sel_trig_inv: C9.1, U3.4
selected_trig: J7.13, U3.3

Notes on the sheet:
length of hold 25k pot
one side to the board, the other to ground
connector to select which one will do the ambient trigger

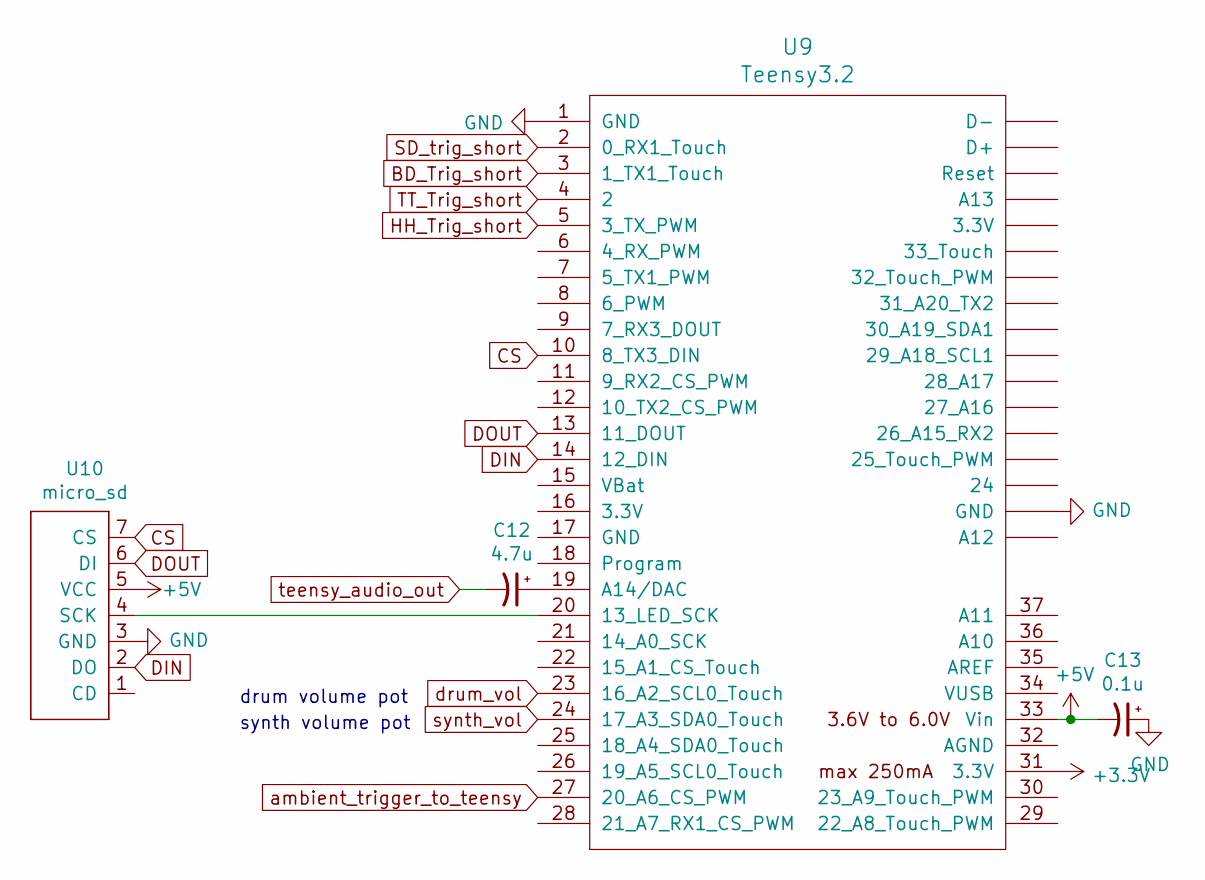
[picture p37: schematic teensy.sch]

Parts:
C12: 4.7u; C_Axial_L3.8mm_D2.6mm_P7.50mm_Horizontal_BIG
C13: 0.1u; C_Axial_L3.8mm_D2.6mm_P7.50mm_Horizontal_BIG
U9: Teensy3.2; Teensy30_31_32_LC_BIG
U10: micro_sd; sparkfun_sd_card

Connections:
+3V3: U9.31 (3.3V); also elsewhere on the board
+5V: C13.2, U9.33 (Vin), U10.5 (VCC); also elsewhere on the board
BD_Trig_short: U9.3 (1_TX1_Touch); also elsewhere on the board
CS: U9.10 (8_TX3_DIN), U10.7 (CS)
DIN: U9.14 (12_DIN), U10.2 (DO)
DOUT: U9.13 (11_DOUT), U10.6 (DI)
GND: C13.1, U9.1 (GND), U9.~ (24), U10.3 (GND); also elsewhere on the board
HH_Trig_short: U9.5 (3_TX_PWM); also elsewhere on the board
unnamed: C12.1, U9.19 (A14/DAC)
unnamed: U9.20 (13_LED_SCK), U10.4 (SCK)
SD_trig_short: U9.2 (0_RX1_Touch); also elsewhere on the board
TT_Trig_short: U9.4 (2); also elsewhere on the board
ambient_trigger_to_teensy: U9.27 (20_A6_CS_PWM); also elsewhere on the board
drum_vol: U9.23 (16_A2_SCL0_Touch); also elsewhere on the board
synth_vol: U9.24 (17_A3_SDA0_Touch); also elsewhere on the board
teensy_audio_out: C12.2; also elsewhere on the board

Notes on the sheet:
drum volume pot
synth volume pot

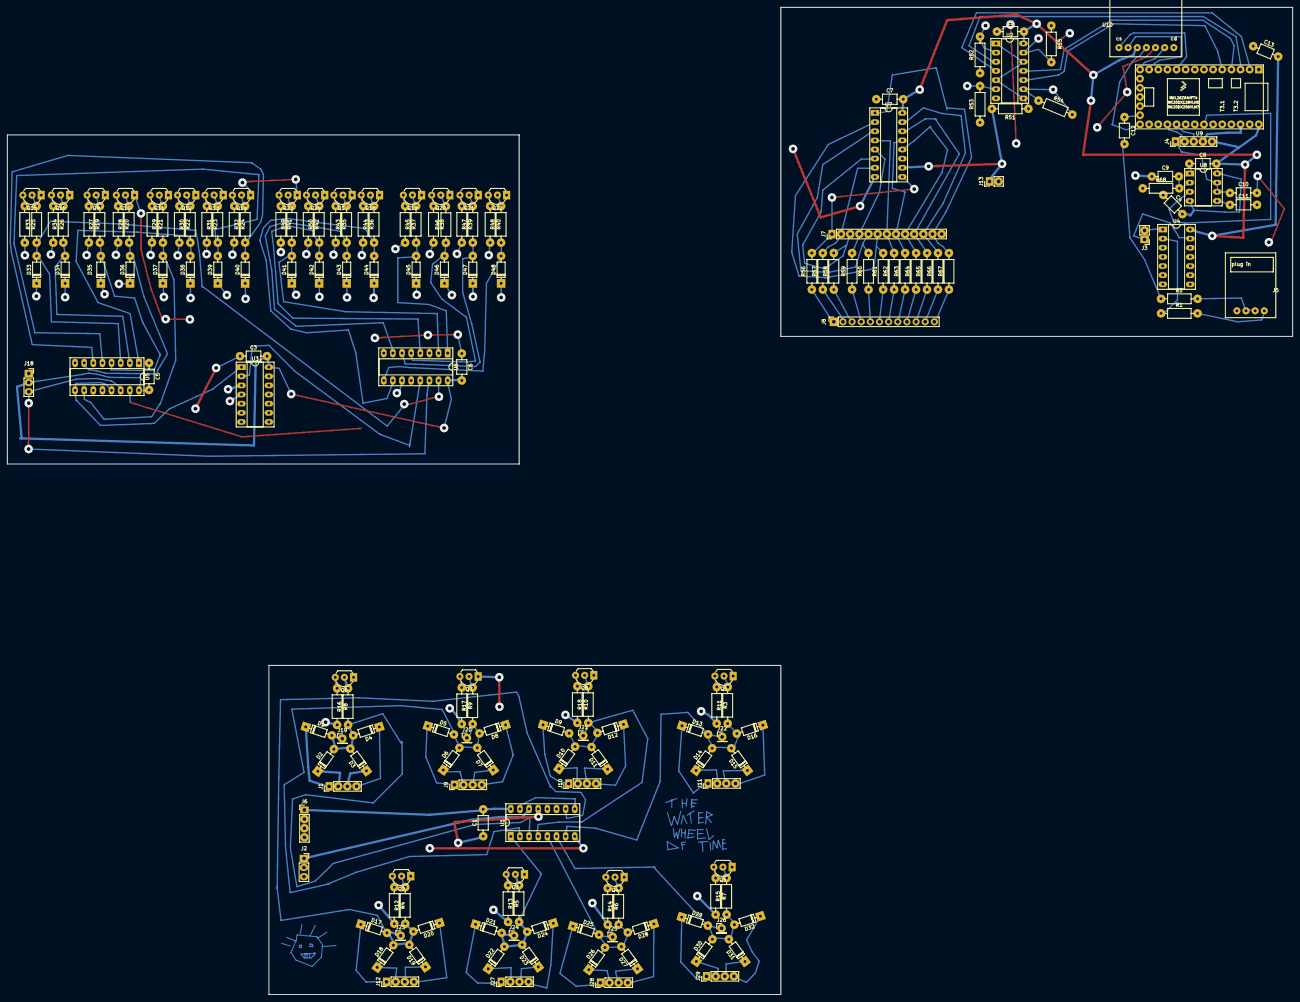
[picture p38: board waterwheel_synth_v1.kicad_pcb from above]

Board: 2 copper layers, 357.2 x 274.3 mm, 188 parts (0 on the bottom side), 164 nets.

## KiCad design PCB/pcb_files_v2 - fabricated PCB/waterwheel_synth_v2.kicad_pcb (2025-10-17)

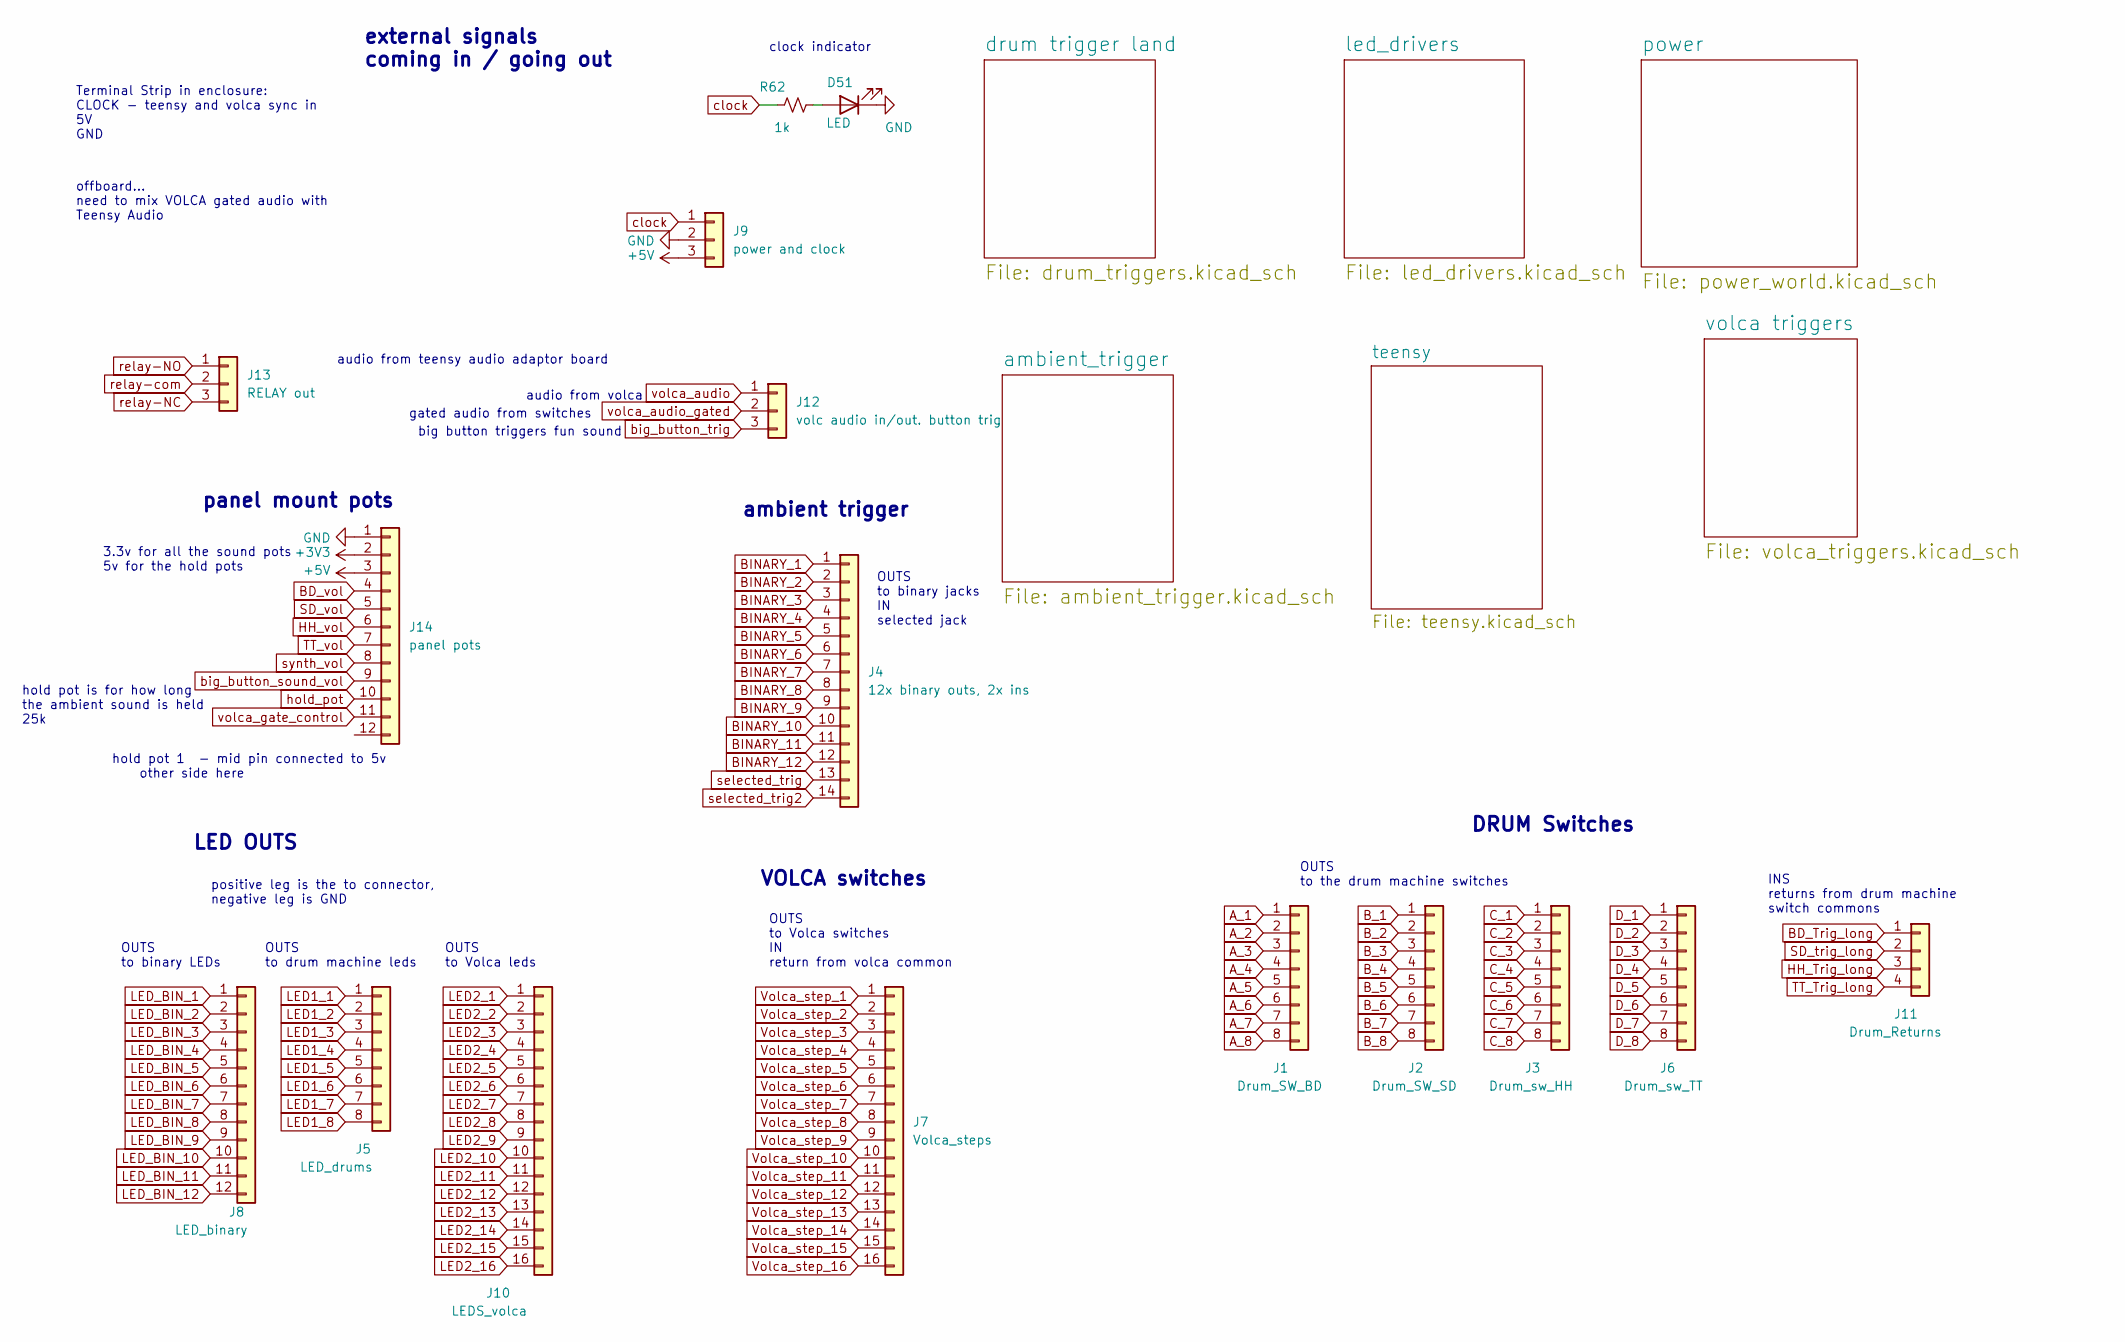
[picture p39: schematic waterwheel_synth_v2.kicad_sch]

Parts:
D51: LED; D_0805_2012Metric; LCSC C84256
J1: Drum_SW_BD; PhoenixContact_MC_1,5_8-G-3.81_1x08_P3.81mm_Horizontal
J2: Drum_SW_SD; PhoenixContact_MC_1,5_8-G-3.81_1x08_P3.81mm_Horizontal
J3: Drum_sw_HH; PhoenixContact_MC_1,5_8-G-3.81_1x08_P3.81mm_Horizontal
J4: 12x binary outs, 2x ins; PhoenixContact_MC_1,5_14-G-3.81_1x14_P3.81mm_Horizontal
J5: LED_drums; PhoenixContact_MC_1,5_8-G-3.81_1x08_P3.81mm_Horizontal
J6: Drum_sw_TT; PhoenixContact_MC_1,5_8-G-3.81_1x08_P3.81mm_Horizontal
J7: Volca_steps; PhoenixContact_MC_1,5_16-G-3.81_1x16_P3.81mm_Horizontal
J8: LED_binary; PhoenixContact_MC_1,5_12-G-3.81_1x12_P3.81mm_Horizontal
J9: power and clock; PhoenixContact_MC_1,5_3-G-3.81_1x03_P3.81mm_Horizontal
J10: LEDS_volca; PhoenixContact_MC_1,5_16-G-3.81_1x16_P3.81mm_Horizontal
J11: Drum_Returns; PhoenixContact_MC_1,5_4-G-3.81_1x04_P3.81mm_Horizontal
J12: volc audio in/out. button trig; PhoenixContact_MC_1,5_3-G-3.81_1x03_P3.81mm_Horizontal
J13: RELAY out; PhoenixContact_MC_1,5_3-G-3.81_1x03_P3.81mm_Horizontal
J14: panel pots; PhoenixContact_MC_1,5_12-G-3.81_1x12_P3.81mm_Horizontal
R62: 1k; R_0603_1608Metric; LCSC C17513

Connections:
+3V3: J14.2; also elsewhere on the board
A_1: J1.1; also elsewhere on the board
A_2: J1.2; also elsewhere on the board
A_3: J1.3; also elsewhere on the board
A_4: J1.4; also elsewhere on the board
A_5: J1.5; also elsewhere on the board
A_6: J1.6; also elsewhere on the board
A_7: J1.7; also elsewhere on the board
A_8: J1.8; also elsewhere on the board
BD_Trig_long: J11.1; also elsewhere on the board
BD_vol: J14.4; also elsewhere on the board
BINARY_1: J4.1; also elsewhere on the board
BINARY_2: J4.2; also elsewhere on the board
BINARY_3: J4.3; also elsewhere on the board
BINARY_4: J4.4; also elsewhere on the board
BINARY_5: J4.5; also elsewhere on the board
BINARY_6: J4.6; also elsewhere on the board
BINARY_7: J4.7; also elsewhere on the board
BINARY_8: J4.8; also elsewhere on the board
BINARY_9: J4.9; also elsewhere on the board
BINARY_10: J4.10; also elsewhere on the board
BINARY_11: J4.11; also elsewhere on the board
BINARY_12: J4.12; also elsewhere on the board
B_1: J2.1; also elsewhere on the board
B_2: J2.2; also elsewhere on the board
B_3: J2.3; also elsewhere on the board
B_4: J2.4; also elsewhere on the board
B_5: J2.5; also elsewhere on the board
B_6: J2.6; also elsewhere on the board
B_7: J2.7; also elsewhere on the board
B_8: J2.8; also elsewhere on the board
C_1: J3.1; also elsewhere on the board
C_2: J3.2; also elsewhere on the board
C_3: J3.3; also elsewhere on the board
C_4: J3.4; also elsewhere on the board
C_5: J3.5; also elsewhere on the board
C_6: J3.6; also elsewhere on the board
C_7: J3.7; also elsewhere on the board
C_8: J3.8; also elsewhere on the board
D_1: J6.1; also elsewhere on the board
D_2: J6.2; also elsewhere on the board
D_3: J6.3; also elsewhere on the board
D_4: J6.4; also elsewhere on the board
D_5: J6.5; also elsewhere on the board
D_6: J6.6; also elsewhere on the board
D_7: J6.7; also elsewhere on the board
D_8: J6.8; also elsewhere on the board
GND: D51.1 (K), J9.2, J14.1; also elsewhere on the board
HH_Trig_long: J11.3; also elsewhere on the board
HH_vol: J14.6; also elsewhere on the board
LED1_1: J5.1; also elsewhere on the board
LED1_2: J5.2; also elsewhere on the board
LED1_3: J5.3; also elsewhere on the board
LED1_4: J5.4; also elsewhere on the board
LED1_5: J5.5; also elsewhere on the board
LED1_6: J5.6; also elsewhere on the board
LED1_7: J5.7; also elsewhere on the board
LED1_8: J5.8; also elsewhere on the board
LED2_1: J10.1; also elsewhere on the board
LED2_2: J10.2; also elsewhere on the board
LED2_3: J10.3; also elsewhere on the board
LED2_4: J10.4; also elsewhere on the board
LED2_5: J10.5; also elsewhere on the board
LED2_6: J10.6; also elsewhere on the board
LED2_7: J10.7; also elsewhere on the board
LED2_8: J10.8; also elsewhere on the board
LED2_9: J10.9; also elsewhere on the board
LED2_10: J10.10; also elsewhere on the board
LED2_11: J10.11; also elsewhere on the board
LED2_12: J10.12; also elsewhere on the board
LED2_13: J10.13; also elsewhere on the board
LED2_14: J10.14; also elsewhere on the board
LED2_15: J10.15; also elsewhere on the board
LED2_16: J10.16; also elsewhere on the board
LED_BIN_1: J8.1; also elsewhere on the board
LED_BIN_2: J8.2; also elsewhere on the board
LED_BIN_3: J8.3; also elsewhere on the board
LED_BIN_4: J8.4; also elsewhere on the board
LED_BIN_5: J8.5; also elsewhere on the board
LED_BIN_6: J8.6; also elsewhere on the board
LED_BIN_7: J8.7; also elsewhere on the board
LED_BIN_8: J8.8; also elsewhere on the board
LED_BIN_9: J8.9; also elsewhere on the board
LED_BIN_10: J8.10; also elsewhere on the board
LED_BIN_11: J8.11; also elsewhere on the board
LED_BIN_12: J8.12; also elsewhere on the board
unnamed: D51.2 (A), R62.1
SD_trig_long: J11.2; also elsewhere on the board
SD_vol: J14.5; also elsewhere on the board
TT_Trig_long: J11.4; also elsewhere on the board
TT_vol: J14.7; also elsewhere on the board
Volca_step_1: J7.1; also elsewhere on the board
Volca_step_2: J7.2; also elsewhere on the board
Volca_step_3: J7.3; also elsewhere on the board
Volca_step_4: J7.4; also elsewhere on the board
Volca_step_5: J7.5; also elsewhere on the board
Volca_step_6: J7.6; also elsewhere on the board
Volca_step_7: J7.7; also elsewhere on the board
Volca_step_8: J7.8; also elsewhere on the board
Volca_step_9: J7.9; also elsewhere on the board
Volca_step_10: J7.10; also elsewhere on the board
Volca_step_11: J7.11; also elsewhere on the board
Volca_step_12: J7.12; also elsewhere on the board
Volca_step_13: J7.13; also elsewhere on the board
Volca_step_14: J7.14; also elsewhere on the board
Volca_step_15: J7.15; also elsewhere on the board
Volca_step_16: J7.16; also elsewhere on the board
big_button_sound_vol: J14.9; also elsewhere on the board
big_button_trig: J12.3; also elsewhere on the board
clock: J9.1, R62.2; also elsewhere on the board
relay-NC: J13.3; also elsewhere on the board
relay-NO: J13.1; also elsewhere on the board
relay-com: J13.2; also elsewhere on the board
selected_trig: J4.13; also elsewhere on the board
selected_trig2: J4.14; also elsewhere on the board
synth_vol: J14.8; also elsewhere on the board
volca_audio: J12.1; also elsewhere on the board
volca_audio_gated: J12.2; also elsewhere on the board
volca_gate_control: J14.11; also elsewhere on the board

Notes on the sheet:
clock indicator
audio from teensy audio adaptor board
VOLCA switches
OUTS to the drum machine switches
positive leg is the to connector, negative leg is GND
gated audio from switches
OUTS to binary jacks IN selected jack
hold pot 1 - mid pin connected to 5v other side here
OUTS to drum machine leds
audio from volca
offboard... need to mix VOLCA gated audio with Teensy Audio
3.3v for all the sound pots 5v for the hold pots
DRUM Switches
INS returns from drum machine switch commons
external signals coming in / going out
OUTS to binary LEDs
Terminal Strip in enclosure: CLOCK - teensy and volca sync in 5V GND
LED OUTS
OUTS to Volca leds
panel mount pots
ambient trigger
OUTS to Volca switches IN return from volca common
big button triggers fun sound
hold pot is for how long the ambient sound is held 25k

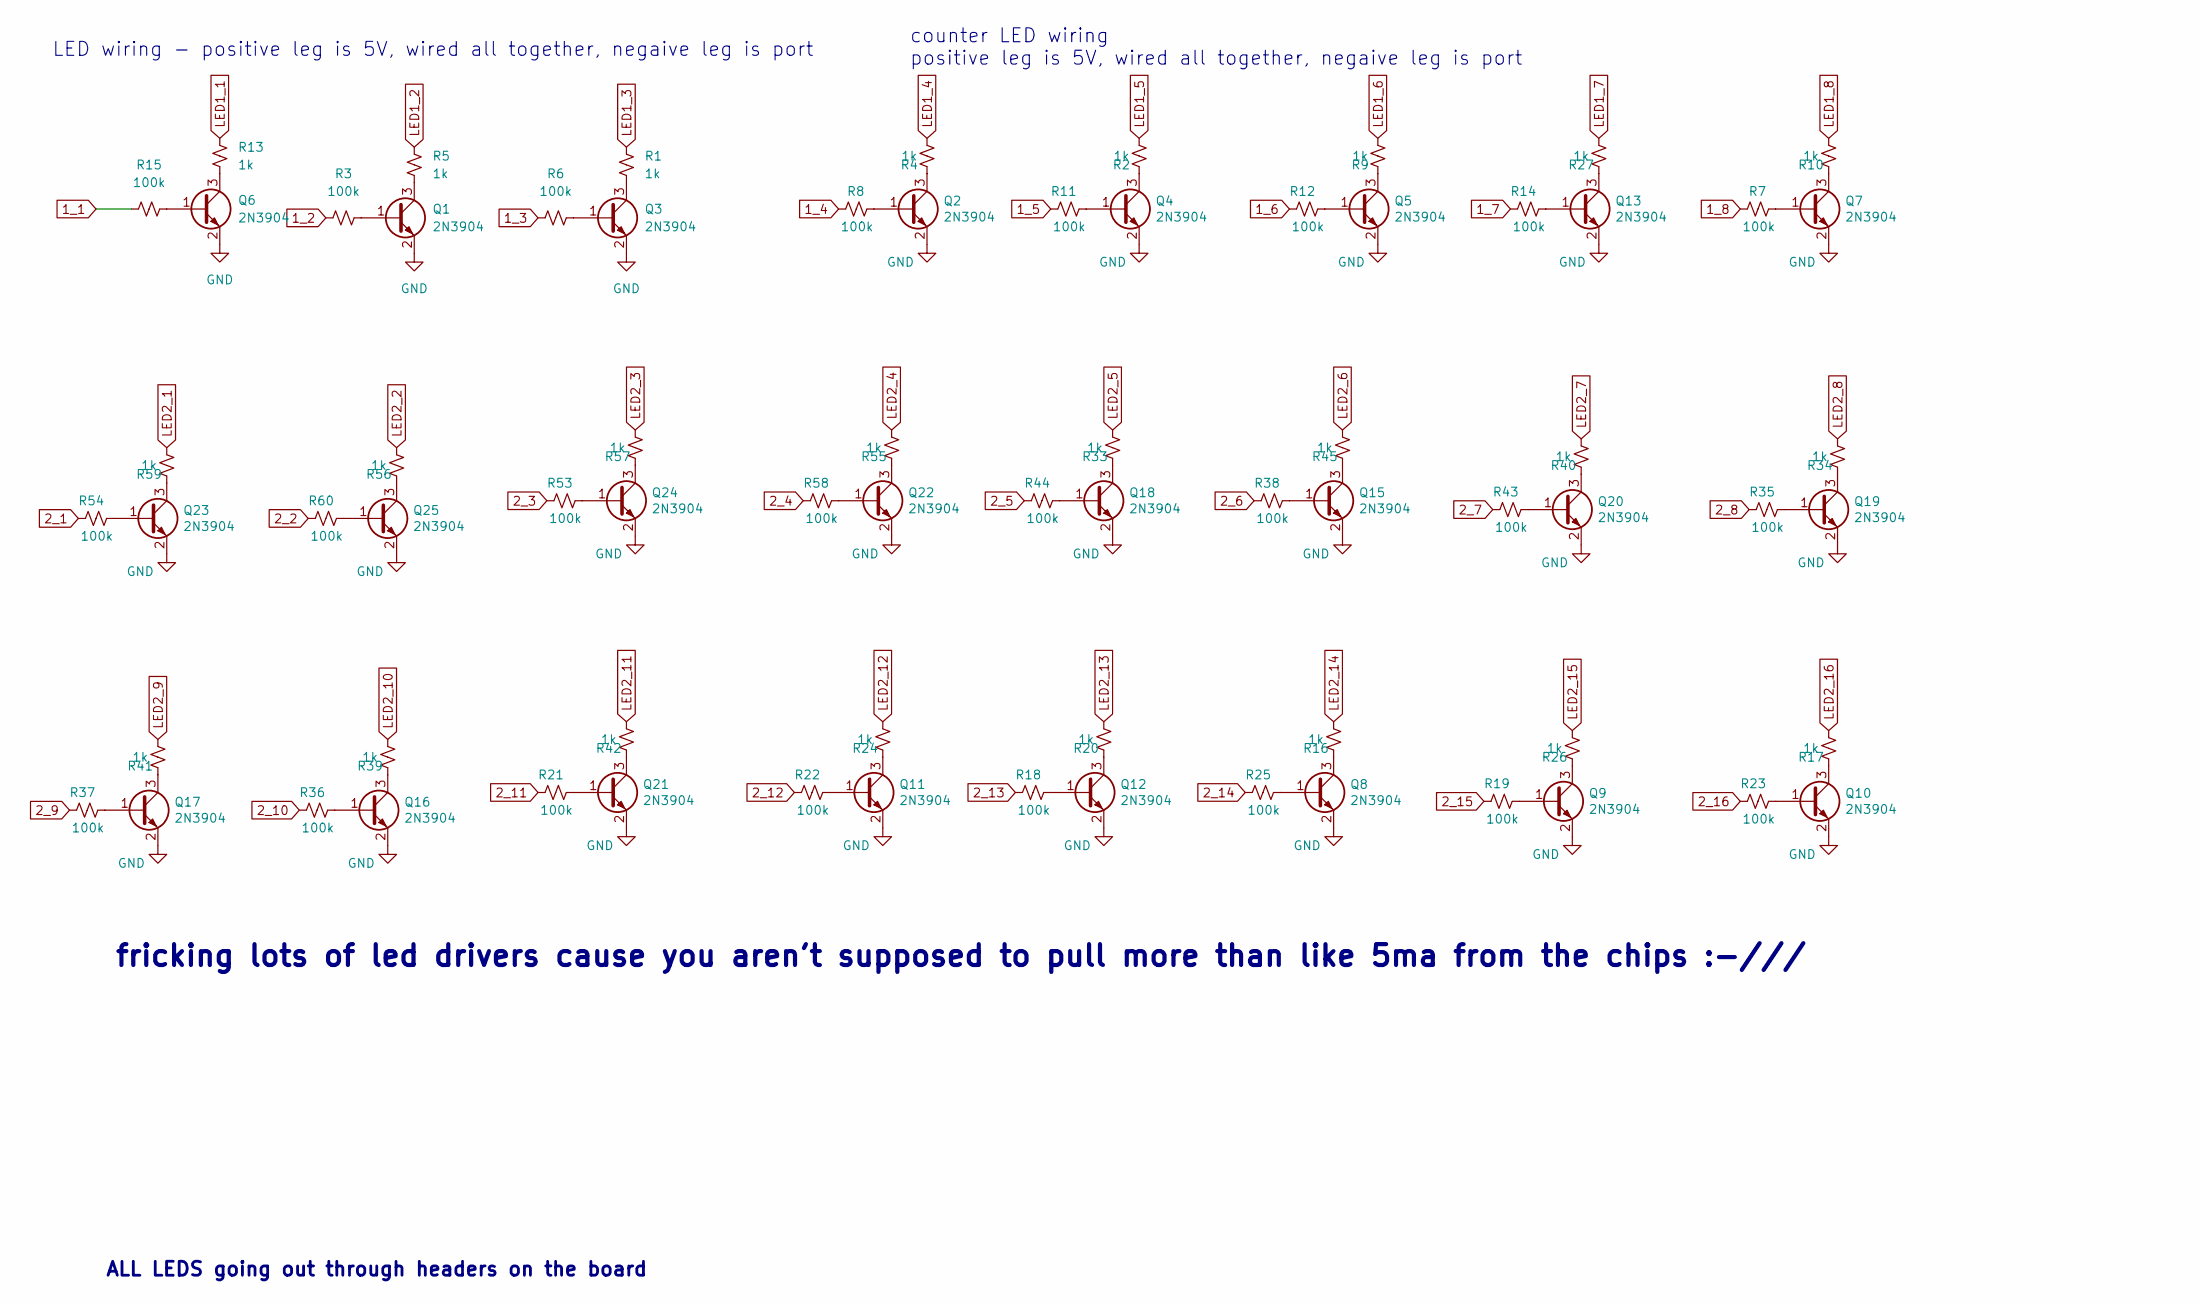
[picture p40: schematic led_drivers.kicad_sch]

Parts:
Q1, Q2, Q3, Q4, Q5, Q6, Q7, Q8, Q9, Q10, Q11, Q12, Q13, Q15, Q16, Q17, Q18, Q19, Q20, Q21, Q22, Q23, Q24, Q25: 2N3904; TSOT-23
R1, R2, R4, R5, R9, R10, R13, R16, R17, R20, R24, R26, R27, R33, R34, R39, R40, R41, R42, R45, R55, R56, R57, R59: 1k; R_0603_1608Metric
R3, R6, R7, R8, R11, R12, R14, R15, R18, R19, R21, R22, R23, R25, R35, R36, R37, R38, R43, R44, R53, R54, R58, R60: 100k; R_0603_1608Metric

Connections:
1_1: R15.1; also elsewhere on the board
1_2: R3.1; also elsewhere on the board
1_3: R6.1; also elsewhere on the board
1_4: R8.1; also elsewhere on the board
1_5: R11.1; also elsewhere on the board
1_6: R12.1; also elsewhere on the board
1_7: R14.1; also elsewhere on the board
1_8: R7.1; also elsewhere on the board
2_1: R54.1; also elsewhere on the board
2_2: R60.1; also elsewhere on the board
2_3: R53.1; also elsewhere on the board
2_4: R58.1; also elsewhere on the board
2_5: R44.1; also elsewhere on the board
2_6: R38.1; also elsewhere on the board
2_7: R43.1; also elsewhere on the board
2_8: R35.1; also elsewhere on the board
2_9: R37.1; also elsewhere on the board
2_10: R36.1; also elsewhere on the board
2_11: R21.1; also elsewhere on the board
2_12: R22.1; also elsewhere on the board
2_13: R18.1; also elsewhere on the board
2_14: R25.1; also elsewhere on the board
2_15: R19.1; also elsewhere on the board
2_16: R23.1; also elsewhere on the board
GND: Q1.2 (E), Q2.2 (E), Q3.2 (E), Q4.2 (E), Q5.2 (E), Q6.2 (E), Q7.2 (E), Q8.2 (E), Q9.2 (E), Q10.2 (E), Q11.2 (E), Q12.2 (E), Q13.2 (E), Q15.2 (E), Q16.2 (E), Q17.2 (E), Q18.2 (E), Q19.2 (E), Q20.2 (E), Q21.2 (E), Q22.2 (E), Q23.2 (E), Q24.2 (E), Q25.2 (E); also elsewhere on the board
LED1_1: R13.2; also elsewhere on the board
LED1_2: R5.2; also elsewhere on the board
LED1_3: R1.2; also elsewhere on the board
LED1_4: R4.2; also elsewhere on the board
LED1_5: R2.2; also elsewhere on the board
LED1_6: R9.2; also elsewhere on the board
LED1_7: R27.2; also elsewhere on the board
LED1_8: R10.2; also elsewhere on the board
LED2_1: R59.2; also elsewhere on the board
LED2_2: R56.2; also elsewhere on the board
LED2_3: R57.2; also elsewhere on the board
LED2_4: R55.2; also elsewhere on the board
LED2_5: R33.2; also elsewhere on the board
LED2_6: R45.2; also elsewhere on the board
LED2_7: R40.2; also elsewhere on the board
LED2_8: R34.2; also elsewhere on the board
LED2_9: R41.2; also elsewhere on the board
LED2_10: R39.2; also elsewhere on the board
LED2_11: R42.2; also elsewhere on the board
LED2_12: R24.2; also elsewhere on the board
LED2_13: R20.2; also elsewhere on the board
LED2_14: R16.2; also elsewhere on the board
LED2_15: R26.2; also elsewhere on the board
LED2_16: R17.2; also elsewhere on the board
unnamed: Q1.1 (B), R3.2
unnamed: Q1.3 (C), R5.1
unnamed: Q2.1 (B), R8.2
unnamed: Q2.3 (C), R4.1
unnamed: Q3.1 (B), R6.2
unnamed: Q3.3 (C), R1.1
unnamed: Q4.1 (B), R11.2
unnamed: Q4.3 (C), R2.1
unnamed: Q5.1 (B), R12.2
unnamed: Q5.3 (C), R9.1
unnamed: Q6.1 (B), R15.2
unnamed: Q6.3 (C), R13.1
unnamed: Q7.1 (B), R7.2
unnamed: Q7.3 (C), R10.1
unnamed: Q8.1 (B), R25.2
unnamed: Q8.3 (C), R16.1
unnamed: Q9.1 (B), R19.2
unnamed: Q9.3 (C), R26.1
unnamed: Q10.1 (B), R23.2
unnamed: Q10.3 (C), R17.1
unnamed: Q11.1 (B), R22.2
unnamed: Q11.3 (C), R24.1
unnamed: Q12.1 (B), R18.2
unnamed: Q12.3 (C), R20.1
unnamed: Q13.1 (B), R14.2
unnamed: Q13.3 (C), R27.1
unnamed: Q15.1 (B), R38.2
unnamed: Q15.3 (C), R45.1
unnamed: Q16.1 (B), R36.2
unnamed: Q16.3 (C), R39.1
unnamed: Q17.1 (B), R37.2
unnamed: Q17.3 (C), R41.1
unnamed: Q18.1 (B), R44.2
unnamed: Q18.3 (C), R33.1
unnamed: Q19.1 (B), R35.2
unnamed: Q19.3 (C), R34.1
unnamed: Q20.1 (B), R43.2
unnamed: Q20.3 (C), R40.1
unnamed: Q21.1 (B), R21.2
unnamed: Q21.3 (C), R42.1
unnamed: Q22.1 (B), R58.2
unnamed: Q22.3 (C), R55.1
unnamed: Q23.1 (B), R54.2
unnamed: Q23.3 (C), R59.1
unnamed: Q24.1 (B), R53.2
unnamed: Q24.3 (C), R57.1
unnamed: Q25.1 (B), R60.2
unnamed: Q25.3 (C), R56.1

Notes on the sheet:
fricking lots of led drivers cause you aren't supposed to pull more than like 5ma from the chips :-///
counter LED wiring positive leg is 5V, wired all together, negaive leg is port
ALL LEDS going out through headers on the board
LED wiring - positive leg is 5V, wired all together, negaive leg is port

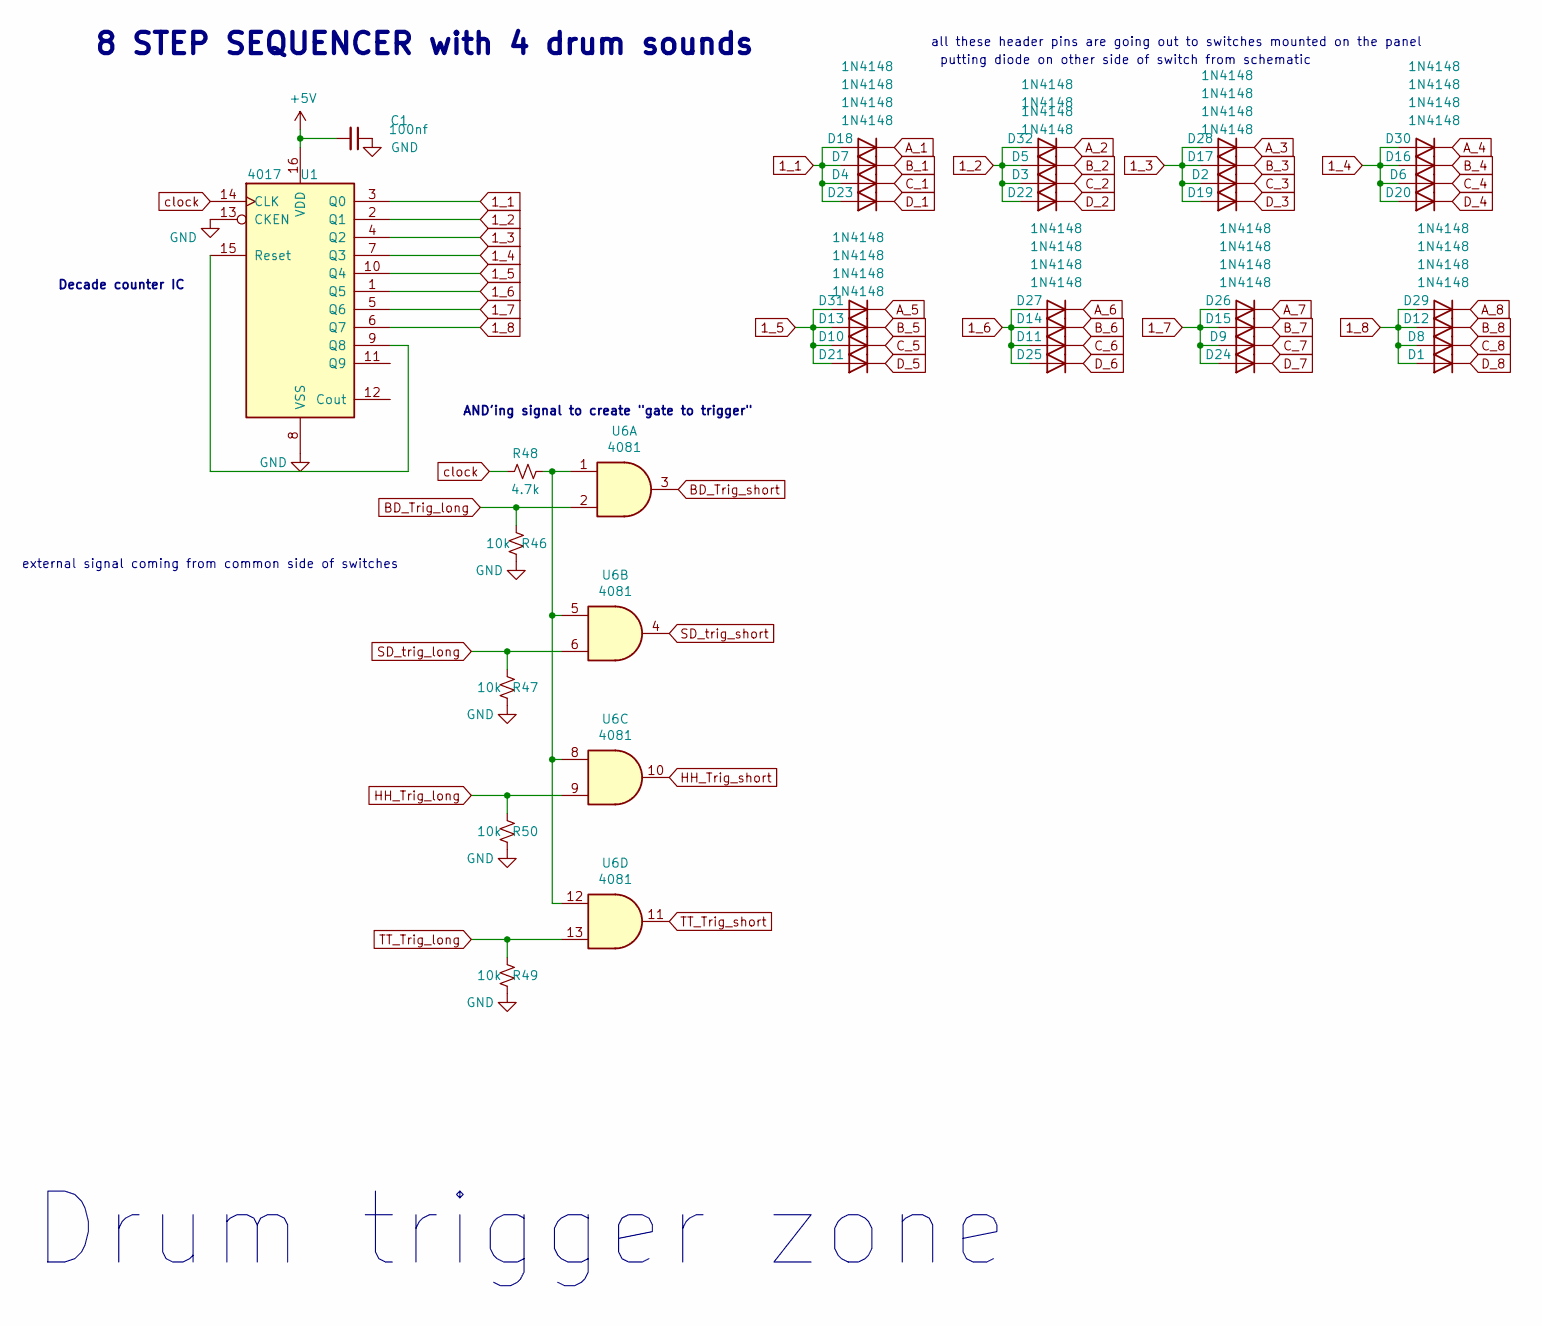
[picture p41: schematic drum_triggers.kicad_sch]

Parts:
C1: 100nf; C_0805_2012Metric
D1, D2, D3, D4, D5, D6, D7, D8, D9, D10, D11, D12, D13, D14, D15, D16, D17, D18, D19, D20, D21, D22, D23, D24, D25, D26, D27, D28, D29, D30, D31, D32: 1N4148; D_SOD-323
R46, R47, R49, R50: 10k; R_0603_1608Metric
R48: 4.7k; R_0603_1608Metric
U1: 4017; SO-16_5.3x10.2mm_P1.27mm
U6: 4081; SO-14_3.9x8.65mm_P1.27mm

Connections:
1_1: D4.2 (A), D7.2 (A), D18.2 (A), D23.2 (A), U1.3 (Q0); also elsewhere on the board
1_2: D3.2 (A), D5.2 (A), D22.2 (A), D32.2 (A), U1.2 (Q1); also elsewhere on the board
1_3: D2.2 (A), D17.2 (A), D19.2 (A), D28.2 (A), U1.4 (Q2); also elsewhere on the board
1_4: D6.2 (A), D16.2 (A), D20.2 (A), D30.2 (A), U1.7 (Q3); also elsewhere on the board
1_5: D10.2 (A), D13.2 (A), D21.2 (A), D31.2 (A), U1.10 (Q4); also elsewhere on the board
1_6: D11.2 (A), D14.2 (A), D25.2 (A), D27.2 (A), U1.1 (Q5); also elsewhere on the board
1_7: D9.2 (A), D15.2 (A), D24.2 (A), D26.2 (A), U1.5 (Q6); also elsewhere on the board
1_8: D1.2 (A), D8.2 (A), D12.2 (A), D29.2 (A), U1.6 (Q7); also elsewhere on the board
A_1: D18.1 (K); also elsewhere on the board
A_2: D32.1 (K); also elsewhere on the board
A_3: D28.1 (K); also elsewhere on the board
A_4: D30.1 (K); also elsewhere on the board
A_5: D31.1 (K); also elsewhere on the board
A_6: D27.1 (K); also elsewhere on the board
A_7: D26.1 (K); also elsewhere on the board
A_8: D29.1 (K); also elsewhere on the board
BD_Trig_long: R46.2, U6.2; also elsewhere on the board
BD_Trig_short: U6.3; also elsewhere on the board
B_1: D7.1 (K); also elsewhere on the board
B_2: D5.1 (K); also elsewhere on the board
B_3: D17.1 (K); also elsewhere on the board
B_4: D16.1 (K); also elsewhere on the board
B_5: D13.1 (K); also elsewhere on the board
B_6: D14.1 (K); also elsewhere on the board
B_7: D15.1 (K); also elsewhere on the board
B_8: D12.1 (K); also elsewhere on the board
C_1: D4.1 (K); also elsewhere on the board
C_2: D3.1 (K); also elsewhere on the board
C_3: D2.1 (K); also elsewhere on the board
C_4: D6.1 (K); also elsewhere on the board
C_5: D10.1 (K); also elsewhere on the board
C_6: D11.1 (K); also elsewhere on the board
C_7: D9.1 (K); also elsewhere on the board
C_8: D8.1 (K); also elsewhere on the board
D_1: D23.1 (K); also elsewhere on the board
D_2: D22.1 (K); also elsewhere on the board
D_3: D19.1 (K); also elsewhere on the board
D_4: D20.1 (K); also elsewhere on the board
D_5: D21.1 (K); also elsewhere on the board
D_6: D25.1 (K); also elsewhere on the board
D_7: D24.1 (K); also elsewhere on the board
D_8: D1.1 (K); also elsewhere on the board
GND: C1.1, R46.1, R47.1, R49.1, R50.1, U1.8 (VSS), U1.13 (CKEN); also elsewhere on the board
HH_Trig_long: R50.2, U6.9; also elsewhere on the board
HH_Trig_short: U6.10; also elsewhere on the board
unnamed: R48.1, U6.1, U6.5, U6.8, U6.12
unnamed: U1.9 (Q8), U1.15 (Reset)
SD_trig_long: R47.2, U6.6; also elsewhere on the board
SD_trig_short: U6.4; also elsewhere on the board
TT_Trig_long: R49.2, U6.13; also elsewhere on the board
TT_Trig_short: U6.11; also elsewhere on the board
clock: R48.2, U1.14 (CLK); also elsewhere on the board

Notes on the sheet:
AND'ing signal to create "gate to trigger"
external signal coming from common side of switches
all these header pins are going out to switches mounted on the panel
8 STEP SEQUENCER with 4 drum sounds
Drum trigger zone
putting diode on other side of switch from schematic
Decade counter IC

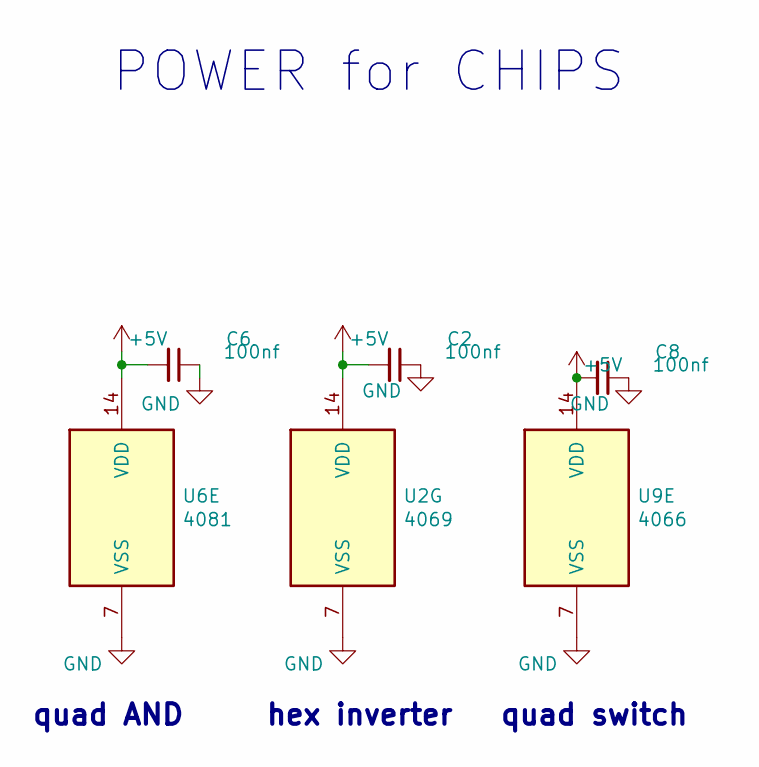
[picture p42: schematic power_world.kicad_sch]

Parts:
C2, C6, C8: 100nf; C_0805_2012Metric
U2: 4069; SO-14_3.9x8.65mm_P1.27mm
U6: 4081; SO-14_3.9x8.65mm_P1.27mm
U9: 4066; SO-14_3.9x8.65mm_P1.27mm

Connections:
GND: C2.1, C6.1, C8.1, U2.7 (VSS), U6.7 (VSS), U9.7 (VSS); also elsewhere on the board

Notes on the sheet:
quad switch
POWER for CHIPS
hex inverter
quad AND


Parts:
C4, C5: 100nf; C_0805_2012Metric
D33, D34, D35, D36, D39, D40, D41, D42, D43, D44, D45, D46, D47, D48, D49, D50: 1N4148; D_SOD-323
U2: 4069; SO-14_3.9x8.65mm_P1.27mm
U4, U7: 4017; SO-16_5.3x10.2mm_P1.27mm
U9: 4066; SO-14_3.9x8.65mm_P1.27mm

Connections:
2_1: D36.2 (A), U4.15 (Reset), U7.3 (Q0); also elsewhere on the board
2_2: D35.2 (A), U7.2 (Q1); also elsewhere on the board
2_3: D33.2 (A), U7.4 (Q2); also elsewhere on the board
2_4: D34.2 (A), U7.7 (Q3); also elsewhere on the board
2_5: D43.2 (A), U7.10 (Q4); also elsewhere on the board
2_6: D40.2 (A), U7.1 (Q5); also elsewhere on the board
2_7: D41.2 (A), U7.5 (Q6); also elsewhere on the board
2_8: D39.2 (A), U7.6 (Q7); also elsewhere on the board
2_9: D42.2 (A), U4.2 (Q1); also elsewhere on the board
2_10: D46.2 (A), U4.4 (Q2); also elsewhere on the board
2_11: D45.2 (A), U4.7 (Q3); also elsewhere on the board
2_12: D44.2 (A), U4.10 (Q4); also elsewhere on the board
2_13: D49.2 (A), U4.1 (Q5); also elsewhere on the board
2_14: D48.2 (A), U4.5 (Q6); also elsewhere on the board
2_15: D50.2 (A), U4.6 (Q7); also elsewhere on the board
2_16: D47.2 (A), U4.9 (Q8); also elsewhere on the board
GND: C4.1, C5.1, U4.3 (Q0), U4.8 (VSS), U7.8 (VSS); also elsewhere on the board
unnamed: U2.1, U7.9 (Q8), U7.13 (CKEN)
unnamed: U2.2, U4.13 (CKEN)
unnamed: U4.11 (Q9), U7.15 (Reset)
Volca_step_1: D36.1 (K); also elsewhere on the board
Volca_step_2: D35.1 (K); also elsewhere on the board
Volca_step_3: D33.1 (K); also elsewhere on the board
Volca_step_4: D34.1 (K); also elsewhere on the board
Volca_step_5: D43.1 (K); also elsewhere on the board
Volca_step_6: D40.1 (K); also elsewhere on the board
Volca_step_7: D41.1 (K); also elsewhere on the board
Volca_step_8: D39.1 (K); also elsewhere on the board
Volca_step_9: D42.1 (K); also elsewhere on the board
Volca_step_10: D46.1 (K); also elsewhere on the board
Volca_step_11: D45.1 (K); also elsewhere on the board
Volca_step_12: D44.1 (K); also elsewhere on the board
Volca_step_13: D49.1 (K); also elsewhere on the board
Volca_step_14: D48.1 (K); also elsewhere on the board
Volca_step_15: D50.1 (K); also elsewhere on the board
Volca_step_16: D47.1 (K); also elsewhere on the board
clock: U4.14 (CLK), U7.14 (CLK); also elsewhere on the board
volca_audio: U9.1; also elsewhere on the board
volca_audio_gated: U9.2; also elsewhere on the board
volca_gate_control: U9.13; also elsewhere on the board

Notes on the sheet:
front panel of volca trigger. 16 switches trigger the step being on/off.
4066 - quad bilateral switch. it gates the volca audio

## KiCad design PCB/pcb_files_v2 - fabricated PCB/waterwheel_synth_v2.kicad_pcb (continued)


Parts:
C3, C9: 4.7u; C_0805_2012Metric
C7: 100nf; C_0805_2012Metric
C10: 0.1u; C_0805_2012Metric
C11: 100u; C_1206_3216Metric
C12: 2.2u; C_0805_2012Metric
D37, D38: 1N4148; D_SOD-323
K1: G5Q-1; Relay_SPDT_Omron-G5Q-1
Q14: 2N3904; TSOT-23
R28, R30, R31: 22k; R_0603_1608Metric
R32: 1k; R_0603_1608Metric
R51, R52, R63, R64, R65, R66, R67, R68, R69, R70, R71, R72: 470; R_0603_1608Metric
R61: 10k; R_0603_1608Metric
U2: 4069; SO-14_3.9x8.65mm_P1.27mm
U5: 4040; SO-16_5.3x10.2mm_P1.27mm
U8: 555(NEW_layout); SOIC-8_3.9x4.9mm_P1.27mm

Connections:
BINARY_1: R52.2, U5.9 (Q0); also elsewhere on the board
BINARY_2: R51.2, U5.7 (Q1); also elsewhere on the board
BINARY_3: R67.2, U5.6 (Q2); also elsewhere on the board
BINARY_4: R68.2, U5.5 (Q3); also elsewhere on the board
BINARY_5: R69.2, U5.3 (Q4); also elsewhere on the board
BINARY_6: R64.2, U5.2 (Q5); also elsewhere on the board
BINARY_7: R66.2, U5.4 (Q6); also elsewhere on the board
BINARY_8: R70.2, U5.13 (Q7); also elsewhere on the board
BINARY_9: R65.2, U5.12 (Q8); also elsewhere on the board
BINARY_10: R63.2, U5.14 (Q9); also elsewhere on the board
BINARY_11: R71.2, U5.15 (Q10); also elsewhere on the board
BINARY_12: R72.2, U5.1 (Q11); also elsewhere on the board
GND: C7.1, C10.2, C11.2, C12.1, D37.2 (A), Q14.2 (E), R28.1, R31.1, R61.1, U5.8 (VSS), U8.1 (GND); also elsewhere on the board
LED_BIN_1: R52.1; also elsewhere on the board
LED_BIN_2: R51.1; also elsewhere on the board
LED_BIN_3: R67.1; also elsewhere on the board
LED_BIN_4: R68.1; also elsewhere on the board
LED_BIN_5: R69.1; also elsewhere on the board
LED_BIN_6: R64.1; also elsewhere on the board
LED_BIN_7: R66.1; also elsewhere on the board
LED_BIN_8: R70.1; also elsewhere on the board
LED_BIN_9: R65.1; also elsewhere on the board
LED_BIN_10: R63.1; also elsewhere on the board
LED_BIN_11: R71.1; also elsewhere on the board
LED_BIN_12: R72.1; also elsewhere on the board
unnamed: C3.1, D37.1 (K), R30.2
unnamed: C9.2, R61.2, U8.2 (TR)
unnamed: C10.1, U8.5 (CV)
unnamed: D38.2 (A), K1.1, Q14.3 (C)
unnamed: Q14.1 (B), R32.1
unnamed: R28.2, R30.1, R32.2
ambient_trigger_to_teensy: U8.3 (Q); also elsewhere on the board
clock: U5.10 (CLK); also elsewhere on the board
relay-NC: K1.4; also elsewhere on the board
relay-NO: K1.3; also elsewhere on the board
relay-com: K1.2; also elsewhere on the board
sel_trig_inv: C9.1, U2.4
selected_trig: U2.3; also elsewhere on the board
selected_trig2: C3.2, R31.2; also elsewhere on the board

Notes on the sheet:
selected_trig = ambient sound on teensy selected_trig2 = mechanical switch chime sound
front panel! these are all 1/4" jacks. patch cable connects the wheel jack to one of the binary counters. selected_trig is the result of that patch
555 circuit determines how long the sound will hold
length of hold 25k pot
takes the 2nd trig input, snags the transient, and uses that to trigger a relay that triggers a chime or some mechanical sound


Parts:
C13: 0.1u; C_0805_2012Metric
U10: Teensy3.2; Teensy30_31_32_LC

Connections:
+3V3: U10.31 (3.3V); also elsewhere on the board
BD_Trig_short: U10.3 (1_TX1_Touch); also elsewhere on the board
BD_vol: U10.21 (14_A0_SCK); also elsewhere on the board
GND: C13.1, U10.1 (GND), U10.~ (D-); also elsewhere on the board
HH_Trig_short: U10.5 (3_TX_PWM); also elsewhere on the board
HH_vol: U10.23 (16_A2_SCL0_Touch); also elsewhere on the board
SD_trig_short: U10.2 (0_RX1_Touch); also elsewhere on the board
SD_vol: U10.22 (15_A1_CS_Touch); also elsewhere on the board
TT_Trig_short: U10.4 (2); also elsewhere on the board
TT_vol: U10.24 (17_A3_SDA0_Touch); also elsewhere on the board
ambient_trigger_to_teensy: U10.7 (5_TX1_PWM); also elsewhere on the board
big_button_sound_vol: U10.26 (19_A5_SCL0_Touch); also elsewhere on the board
big_button_trig: U10.6 (4_RX_PWM); also elsewhere on the board
synth_vol: U10.25 (18_A4_SDA0_Touch); also elsewhere on the board

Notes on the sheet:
drum volume pots
Using teensy to play drum samples, synth sounds, and fun trigger sound with big button. Using the Teensy Audio Shield for audio output. Also SD card on audio shield will contain the samples. Audio output is from 1/8" jack on audio shield

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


Board: 2 copper layers, 171.7 x 171.7 mm, 184 parts (16 on the bottom side), 210 nets.

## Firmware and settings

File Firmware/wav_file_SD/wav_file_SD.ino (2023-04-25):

// Simple WAV file player example
//
// Three types of output may be used, by configuring the code below.
//
//   1: Digital I2S - Normally used with the audio shield:
//         http://www.pjrc.com/store/teensy3_audio.html
//
//   2: Digital S/PDIF - Connect pin 22 to a S/PDIF transmitter
//         https://www.oshpark.com/shared_projects/KcDBKHta
//
//   3: Analog DAC - Connect the DAC pin to an amplified speaker
//         http://www.pjrc.com/teensy/gui/?info=AudioOutputAnalog
//
// To configure the output type, first uncomment one of the three
// output objects.  If not using the audio shield, comment out
// the sgtl5000_1 lines in setup(), so it does not wait forever
// trying to configure the SGTL5000 codec chip.
//
// The SD card may connect to different pins, depending on the
// hardware you are using.  Uncomment or configure the SD card
// pins to match your hardware.
//
// Data files to put on your SD card can be downloaded here:
//   http://www.pjrc.com/teensy/td_libs_AudioDataFiles.html
//
// This example code is in the public domain.

#include <Audio.h>
#include <Wire.h>
#include <SPI.h>
#include <SD.h>
#include <SerialFlash.h>

AudioPlaySdWav           playWav1;
// Use one of these 3 output types: Digital I2S, Digital S/PDIF, or Analog DAC
//AudioOutputI2S           audioOutput;
//AudioOutputSPDIF       audioOutput;
AudioOutputAnalog      audioOutput;
AudioConnection          patchCord1(playWav1, 0, audioOutput, 0);
AudioConnection          patchCord2(playWav1, 1, audioOutput, 1);
AudioControlSGTL5000     sgtl5000_1;

// Use these with the Teensy Audio Shield
//#define SDCARD_CS_PIN    10
//#define SDCARD_MOSI_PIN  7
//#define SDCARD_SCK_PIN   14

// Use these with the Teensy 3.5 & 3.6 SD card
//#define SDCARD_CS_PIN    BUILTIN_SDCARD
//#define SDCARD_MOSI_PIN  11  // not actually used
//#define SDCARD_SCK_PIN   13  // not actually used

// Use these for the SD+Wiz820 or other adaptors
#define SDCARD_CS_PIN    8
#define SDCARD_MOSI_PIN  11
#define SDCARD_SCK_PIN   13

void setup() {
  Serial.begin(9600);

  // Audio connections require memory to work.  For more
  // detailed information, see the MemoryAndCpuUsage example
  AudioMemory(8);

  // Comment these out if not using the audio adaptor board.
  // This may wait forever if the SDA & SCL pins lack
  // pullup resistors
//  sgtl5000_1.enable();
//  sgtl5000_1.volume(0.5);

  SPI.setMOSI(SDCARD_MOSI_PIN);
  SPI.setSCK(SDCARD_SCK_PIN);
  if (!(SD.begin(SDCARD_CS_PIN))) {
    // stop here, but print a message repetitively
    while (1) {
      Serial.println("Unable to access the SD card");
      delay(500);
    }
  }
}

void playFile(const char *filename)
{
  Serial.print("Playing file: ");
  Serial.println(filename);

  // Start playing the file.  This sketch continues to
  // run while the file plays.
  playWav1.play(filename);

  // A brief delay for the library read WAV info
  delay(5);

  // Simply wait for the file to finish playing.
  while (playWav1.isPlaying()) {
    // uncomment these lines if you audio shield
    // has the optional volume pot soldered
    //float vol = analogRead(15);
    //vol = vol / 1024;
    // sgtl5000_1.volume(vol);
  }
}


void loop() {
  playFile("BD.WAV");  // filenames are always uppercase 8.3 format
  delay(500);
  playFile("SD.WAV");
  delay(500);
  playFile("HH.WAV");
  delay(500);
  playFile("TT.WAV");
  delay(1500);
}

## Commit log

2023-04-25 updated 555 footprint, it was too big
    [ambient_trigger.kicad_sch, teensy.kicad_sch, waterwheel_synth_v2.kicad_pcb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]
2023-05-03 adding pdf schematic
    [waterwheel_synth_v2.ods]
2025-10-17 oct 2025 update
    [Metal_piece_cutouts.dxf, ambient_trigger.kicad_sch, drum_triggers.kicad_sch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]
2025-11-13 re-organizing folder structure
    [BOM-waterwheel_synth_v2.csv, Metal_piece_cutouts.dxf, ambient_trigger.kicad_sch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]
2025-11-13 updating readme and adding pcb images
